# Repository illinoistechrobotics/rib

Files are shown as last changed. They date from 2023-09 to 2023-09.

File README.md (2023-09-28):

# Illinois Tech Robotics - Robot Interface Board (RIB)

This is a PCB design based around the existing Goliath protoboards, but adapted to work with a Raspberry Pi Pico (W), but is also usable with other robot designs using solder bridge jumpers to support various configurations. 

# Features

## Output
The majority of the circuitry allows connecting 2 OSMC's (Open Source Motor Controller) v3.22 over RJ45. They are wired with pin 2 through 9, as CAT6 only has 8 conductors and pin 1 and 10 are the same as 2 and 9 respectively, in this case we don't need the increased current offered by the extra pins.

The 10 connections for the OSMCs are just PWM or digital outputs using MCT9001 Optocouplers, by default set up for 12V (Or whatever is supplied to VIN), but with a jumper it can be set to 5V or 3.3V logic to interface with a variety of motor controllers.

There is a MAX6959 36-channel LED driver chip, that independently controls the 2-digit 7-segment display, the status LEDs of the ethernet ports, and the 3 RGB LEDs present.

## Input
2 rotary quadrature encoders can be connected with RJ45, intended to be used with the Pico's PIO. The RJ45 connections for the encoders have breakouts for Z inputs (for absolute positioning) or 2 more encoders with relative positioning only. These inputs are not connected to the Pico by default due to the limited number of GPIO pins.

There is a MCP3008 ADC which is used for battery voltage & current monitoring.

## I/O

There are 2 PCF8574 I/O expanders which are mostly ununsed, allowing for the connection of low bandwith devices (e.g. enable pins, end stops / limit switches, basic on/off logic) as their speed is limited by the I2C bus. That said, the interrupt pins are broken out and can be optionally used for a decent connection for a rotary encoder.

The first I/O expander is connected to 2 N-channel MOSFETs that are connected to the board's input voltage for VIN @ 2A (total) controllable high-power output.

There are 3 extra GPIO pins exposed, which can be used for connecting e.g. the extra encoder pins, the I/O expander interrupts, or I2C communication to other RIB(s) in order to create a megaRIB for connecting more than 2 OSMCs.

Finally, there is a place for a Digi xBee to sit and communicate with the robot over 2.4Ghz / 900 MHz radio.

## POWER 

Additionally, the PCB pulls power in from the OSMCs over the RJ45 connections or the top left terminal block. The RIB can take in from 8 to 60V of power, or you can provide 5V via headers directly. If it's necessary, the RIB can be powered by a 2S Lithium battery, the power supply can still function at around 7V in.

The onboard 5V switching power supply can provide ~1.8A and the 3v3 regulator, which pulls from the 5V line, can use up to the same 1.8A limit. The 3v3 regulator exists to  provide extra power to the xBee and 3v3 logic without having to put strain on the Pico.

The power inputs on the OSMC RJ45's can also be changed to *output* power and will match the logic voltage 5V/3.3V.

# Programming

The Pi Pico W can be programming with [Arduino-Pico](https://arduino-pico.readthedocs.io/en/latest/), the Pico C++ SDK, Micro/CircuitPython, or Embassy Rust framework. Code examples below are written based on the Arduino-Pico framework. *Note: we discovered a bug in Arduino-Pico's setXX functions affecting the RIB that is only fixed in v3.6.0 or higher.*

Things to know for programming the hardware on the RIB:

The xBee is connected to UART0 / Serial1 on the Pico via pins 16 & 17 for TX & RX respectively. 

	Serial1.setRX(17);
  	Serial1.setTX(16);

The I2C bus for the LED driver and I/O expanders is connected to I2C1 / Wire, pins 20 & 21 for SDA and SCL respectively. 

    Wire.setSDA(20);
    Wire.setSCL(21);

The LED driver has address 0x38. There is no library for the MAX6959 available online, we wrote one in [rib-test-code](https://git.myitr.org/adeck/rib-test-code). Look for lines like `Wire.beginTransmission(0x38)` and functions like `set_digit()` for example.

The I/O expanders have addresses 0x20 for the top one (connected to MOSFETs) and 0x21 for the bottom one.

The library `xreef/PCF8574` has the ability to set pins as well, so the code you would use is

    PCF8574 ioex1(0x20, 20, 21);
    PCF8574 ioex2(0x21, 20, 21);

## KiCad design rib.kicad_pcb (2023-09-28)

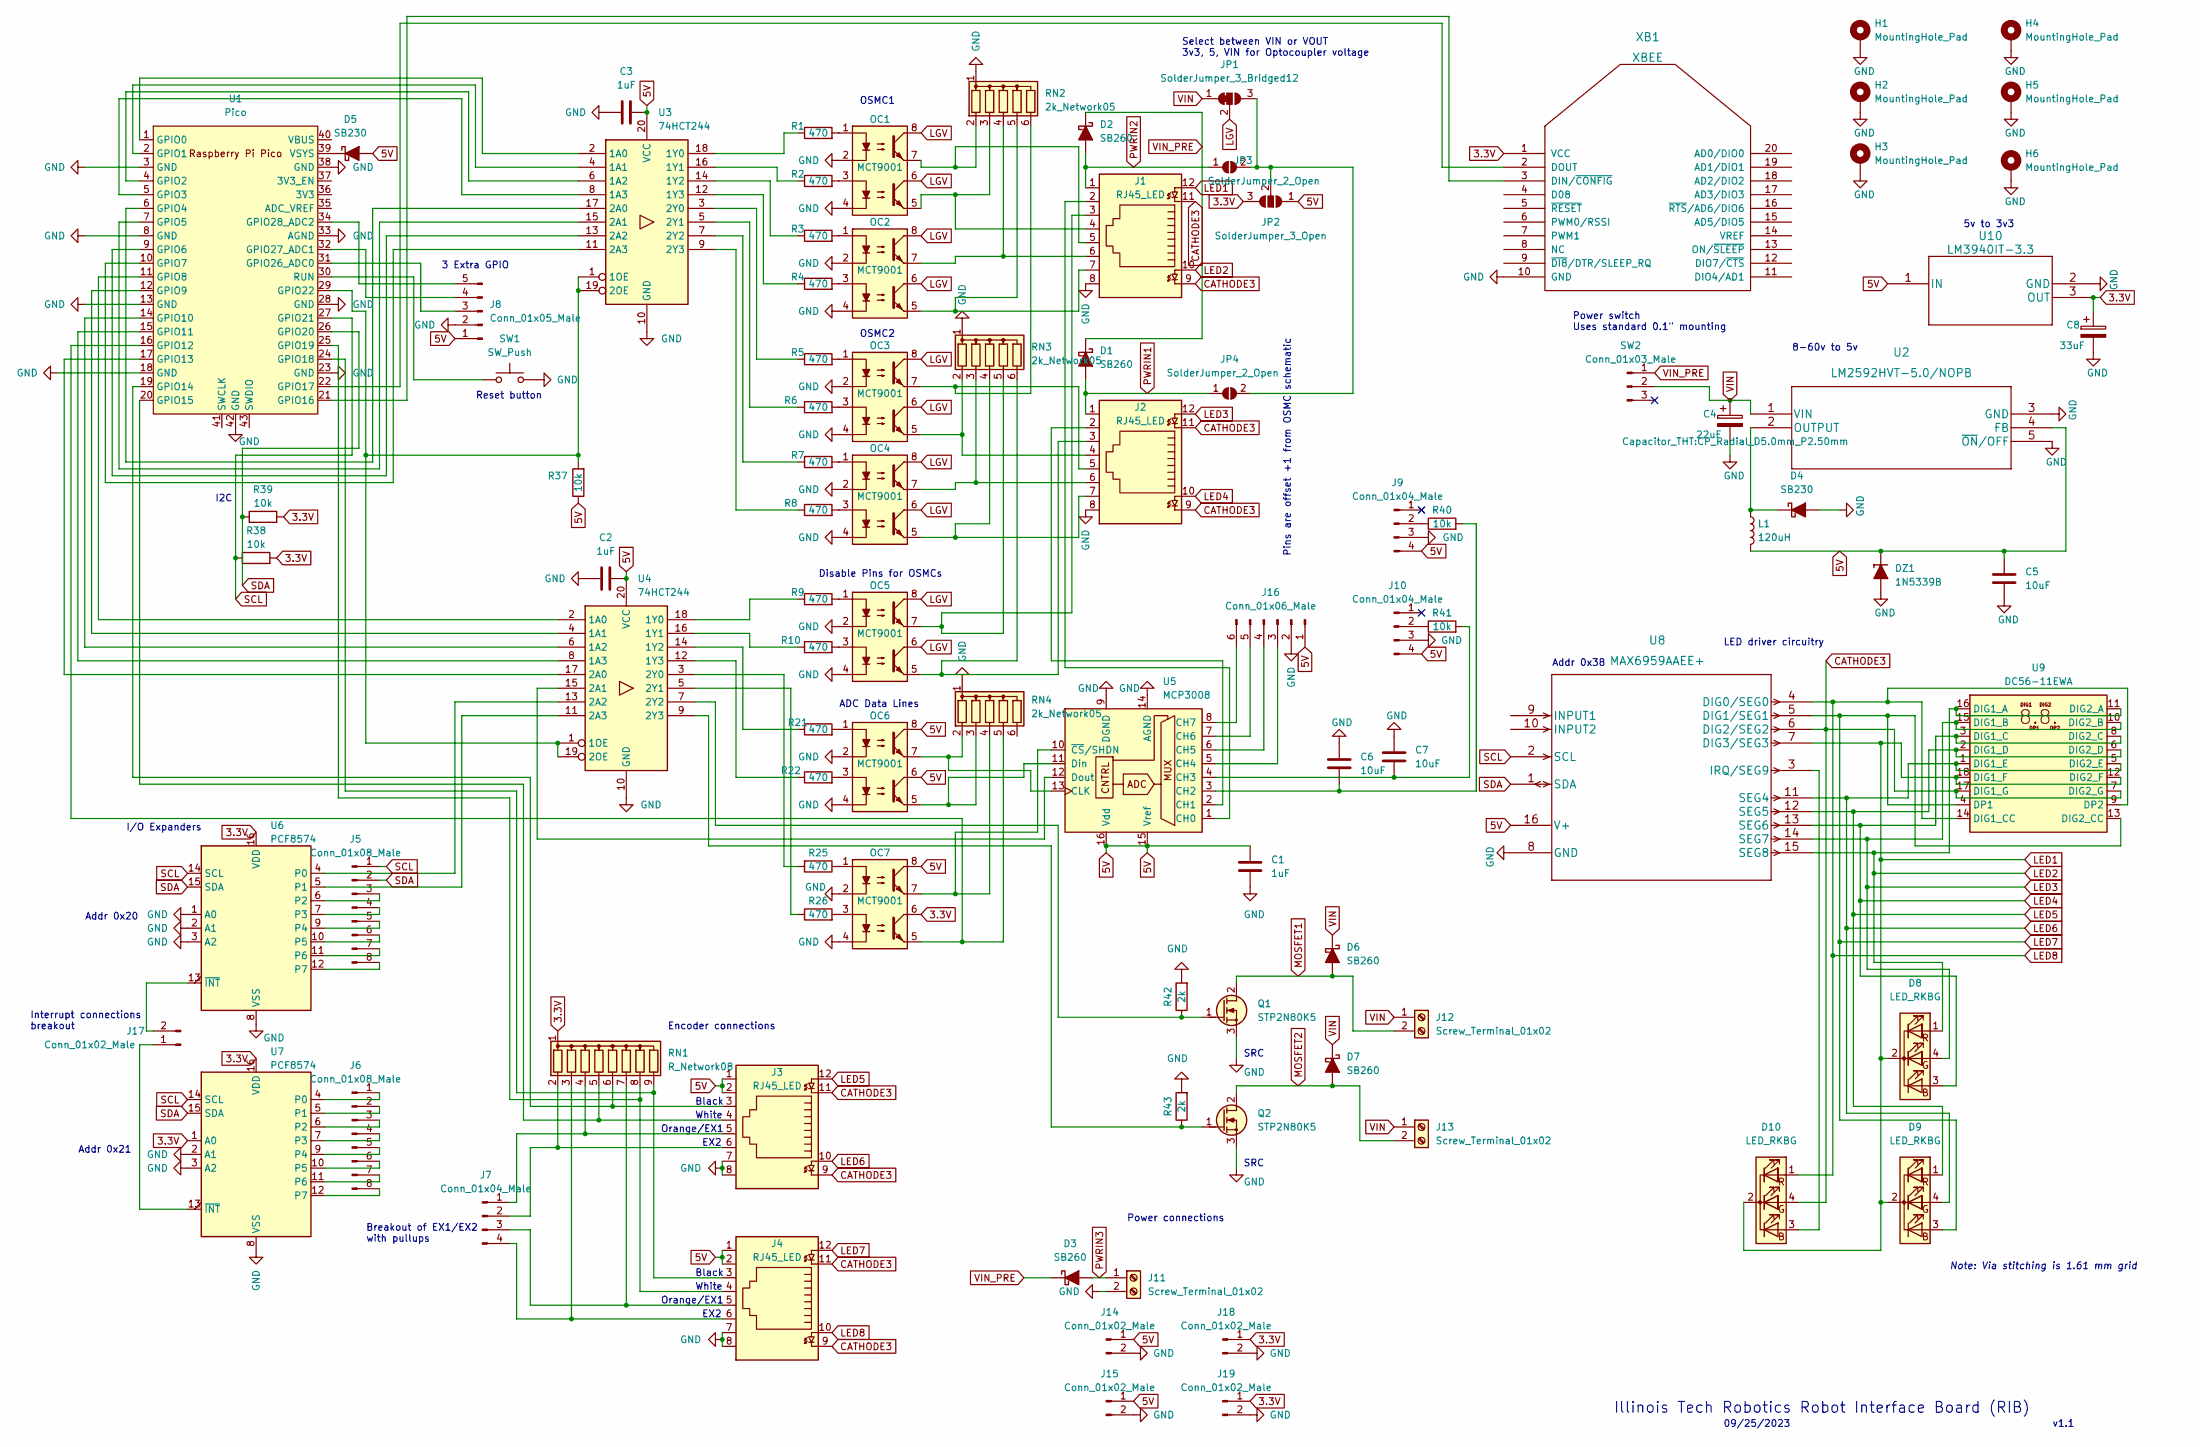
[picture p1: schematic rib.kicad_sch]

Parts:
C1, C2, C3: 1uF; C_Rect_L7.0mm_W4.5mm_P5.00mm
C4: 22uF; CP_Radial_D5.0mm_P2.50mm
C5, C6, C7: 10uF; C_Rect_L7.0mm_W4.5mm_P5.00mm
C8: 33uF; CP_Radial_D5.0mm_P2.50mm
D1, D2, D3, D6, D7: SB260; D_DO-15_P10.16mm_Horizontal
D4, D5: SB230; D_DO-15_P10.16mm_Horizontal
D8, D9, D10: LED_RKBG; LED_D5.0mm-4_RGB_Staggered_Pins
DZ1: 1N5339B; D_5W_CASE-017AA_P12.70mm_Horizontal_Zener
H1, H2, H3, H4, H5, H6: MountingHole_Pad; MountingHole_4.3mm_M4_Pad_Via
J1, J2, J3, J4: RJ45_LED; RJ45_Amphenol_RJHSE538X
J5, J6: Conn_01x08_Male; PinHeader_1x08_P2.54mm_Vertical
J7, J9, J10: Conn_01x04_Male; PinHeader_1x04_P2.54mm_Vertical
J8: Conn_01x05_Male; PinHeader_1x05_P2.54mm_Vertical
J11, J12, J13: Screw_Terminal_01x02; TerminalBlock_Phoenix_MKDS-1,5-2_1x02_P5.00mm_Horizontal
J14, J15, J17, J18, J19: Conn_01x02_Male; PinHeader_1x02_P2.54mm_Vertical
J16: Conn_01x06_Male; PinHeader_1x06_P2.54mm_Vertical
JP1: SolderJumper_3_Bridged12; SolderJumper-3_P1.3mm_Open_Pad1.0x1.5mm
JP2: SolderJumper_3_Open; SolderJumper-3_P1.3mm_Open_Pad1.0x1.5mm
JP3, JP4: SolderJumper_2_Open; SolderJumper-2_P1.3mm_Open_Pad1.0x1.5mm
L1: 120uH; L_Radial_D12.5mm_P7.00mm_Fastron_09HCP
OC1, OC2, OC3, OC4, OC5, OC6, OC7: MCT9001; DIP-8_W7.62mm_Socket
Q1, Q2: STP2N80K5; TO-220-3_Vertical_GDS
R1, R2, R3, R4, R5, R6, R7, R8, R9, R10, R21, R22, R25, R26: 470; R_Axial_DIN0207_L6.3mm_D2.5mm_P10.16mm_Horizontal
R37, R38, R39, R40, R41: 10k; R_Axial_DIN0207_L6.3mm_D2.5mm_P10.16mm_Horizontal
R42, R43: 2k; R_Axial_DIN0207_L6.3mm_D2.5mm_P10.16mm_Horizontal
RN1: R_Network08; R_Array_SIP9
RN2, RN3, RN4: 2k_Network05; R_Array_SIP6
SW1: SW_Push; SW_Tactile_PUSH_4.5mm_H3.8mm_TS_C016
SW2: Conn_01x03_Male; PinSocket_1x03_P2.54mm_Vertical
U1: Pico; RPi_Pico_SMD_TH
U2: LM2592HVT-5.0/NOPB; LM2592HVT-5.0&slash_NOPB
U3, U4: 74HCT244; DIP-20_W7.62mm_Socket
U5: MCP3008; DIP-16_W7.62mm_Socket
U6, U7: PCF8574; DIP-16_W7.62mm_Socket
U8: MAX6959AAEE+; DIP-16_W7.62mm_Socket
U9: DC56-11EWA; DA56-11SURKWA
U10: LM3940IT-3.3; TO-220-3_Vertical
XB1: XBEE; XBEE_PRO_PTH

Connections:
3.3V: C8.1, J18.1, J19.1, JP2.3 (B), OC7.6, R38.2, R39.2, RN1.1 (common), U6.16 (VDD), U7.1 (A0), U7.16 (VDD), U10.3 (OUT), XB1.1 (VCC)
5V: C1.1, C2.2, C3.2, C5.1, D5.2 (A), DZ1.1 (K), J3.1, J3.2, J4.1, J4.2, J8.1, J9.4, J10.4, J14.1, J15.1, J16.1, JP2.1 (A), L1.2, OC6.6, OC6.8, OC7.8, R37.1, U2.4 (FB), U3.20 (VCC), U4.20 (VCC), U5.15 (Vref), U5.16 (Vdd), U8.16 (V+), U10.1 (IN)
CATHODE3: D10.4 (GA), J1.9, J1.11, J2.9, J2.11, J3.9, J3.11, J4.9, J4.11, U8.6 (DIG2/SEG2), U9.7 (DIG2_G), U9.17 (DIG1_G)
GND: C1.2, C2.1, C3.1, C4.2, C5.2, C6.1, C7.1, C8.2, D4.2 (A), DZ1.2 (A), H1.1, H2.1, H3.1, H4.1, H5.1, H6.1, J1.8, J2.8, J3.7, J3.8, J4.7, J4.8, J8.2, J9.3, J10.3, J11.2, J14.2, J15.2, J16.2, J18.2, J19.2, OC1.2, OC1.4, OC2.2, OC2.4, OC3.2, OC3.4, OC4.2, OC4.4, OC5.2, OC5.4, OC6.2, OC6.4, OC7.2, OC7.4, Q1.3 (S), Q2.3 (S), R42.2, R43.2, RN2.1 (common), RN3.1 (common), RN4.1 (common), SW1.2, U1.3 (GND), U1.8 (GND), U1.13 (GND), U1.18 (GND), U1.23 (GND), U1.28 (GND), U1.33 (AGND), U1.38 (GND), U1.42 (GND), U2.3 (GND), U2.5 (~ON/OFF), U3.10 (GND), U4.10 (GND), U5.9 (DGND), U5.14 (AGND), U6.1 (A0), U6.2 (A1), U6.3 (A2), U6.8 (VSS), U7.2 (A1), U7.3 (A2), U7.8 (VSS), U8.8 (GND), U10.2 (GND), XB1.10 (GND)
LED1: D8.2 (K), D9.2 (K), D10.2 (K), J1.12, U8.7 (DIG3/SEG3), U9.12 (DIG2_F), U9.18 (DIG1_F)
LED2: D8.1 (RA), J1.10, U8.15 (SEG8), U9.11 (DIG2_A), U9.16 (DIG1_A)
LED3: D8.4 (GA), J2.12, U8.14 (SEG7), U9.10 (DIG2_B), U9.15 (DIG1_B)
LED4: D8.3 (BA), J2.10, U8.13 (SEG6), U9.3 (DIG1_C), U9.8 (DIG2_C)
LED5: D9.1 (RA), J3.12, U8.12 (SEG5), U9.2 (DIG1_D), U9.6 (DIG2_D)
LED6: D9.4 (GA), J3.10, U8.11 (SEG4), U9.1 (DIG1_E), U9.5 (DIG2_E)
LED7: D9.3 (BA), J4.12, U8.5 (DIG1/SEG1), U9.4 (DP1), U9.13 (DIG2_CC)
LED8: D10.1 (RA), J4.10, U8.4 (DIG0/SEG0), U9.9 (DP2), U9.14 (DIG1_CC)
LGV: JP1.2 (C), OC1.6, OC1.8, OC2.6, OC2.8, OC3.6, OC3.8, OC4.6, OC4.8, OC5.6, OC5.8
MOSFET1: D6.2 (A), J12.2, Q1.2 (D)
MOSFET2: D7.2 (A), J13.2, Q2.2 (D)
unnamed: D4.1 (K), L1.1, U2.2 (OUTPUT)
unnamed: D5.1 (K), U1.39 (VSYS)
unnamed: D10.3 (BA), U8.3 (IRQ/SEG9)
unnamed: J5.3, U6.6 (P2)
unnamed: J5.4, U6.7 (P3)
unnamed: J5.5, U6.9 (P4)
unnamed: J5.6, U6.10 (P5)
unnamed: J5.7, U6.11 (P6)
unnamed: J5.8, U6.12 (P7)
unnamed: J6.1, U7.4 (P0)
unnamed: J6.2, U7.5 (P1)
unnamed: J6.3, U7.6 (P2)
unnamed: J6.4, U7.7 (P3)
unnamed: J6.5, U7.9 (P4)
unnamed: J6.6, U7.10 (P5)
unnamed: J6.7, U7.11 (P6)
unnamed: J6.8, U7.12 (P7)
unnamed: J3.5, J7.1, RN1.4 (R3)
unnamed: J3.6, J7.2, RN1.2 (R1)
unnamed: J4.5, J7.3, RN1.7 (R6)
unnamed: J4.6, J7.4, RN1.3 (R2)
unnamed: J8.3, U1.31 (GPIO26_ADC0)
unnamed: J8.4, U1.32 (GPIO27_ADC1)
unnamed: J8.5, U1.34 (GPIO28_ADC2)
unnamed: J9.2, R40.1
unnamed: J10.2, R41.1
unnamed: J16.3, U5.5 (CH4)
unnamed: J16.4, U5.6 (CH5)
unnamed: J16.5, U5.7 (CH6)
unnamed: J16.6, U5.8 (CH7)
unnamed: J17.1, U7.13 (~INT)
unnamed: J17.2, U6.13 (~INT)
unnamed: JP1.3 (B), JP2.2 (C), JP3.2 (B), JP4.2 (B)
unnamed: OC1.1, R1.2
unnamed: OC1.3, R2.2
unnamed: OC2.1, R3.2
unnamed: OC2.3, R4.2
unnamed: OC3.1, R5.2
unnamed: OC3.3, R6.2
unnamed: OC4.1, R7.2
unnamed: OC4.3, R8.2
unnamed: OC5.1, R9.2
unnamed: OC5.3, R10.2
unnamed: OC6.1, R21.2
unnamed: OC6.3, R22.2
unnamed: OC7.1, R25.1
unnamed: OC7.3, R26.2
unnamed: Q1.1 (G), R42.1, U4.7 (2Y2)
unnamed: Q2.1 (G), R43.1, U4.9 (2Y3)
unnamed: J3.4, RN1.5 (R4), U1.20 (GPIO15)
unnamed: J3.3, RN1.6 (R5), U1.19 (GPIO14)
unnamed: J4.4, RN1.8 (R7), U1.25 (GPIO19)
unnamed: J4.3, RN1.9 (R8), U1.24 (GPIO18)
unnamed: J1.5, OC1.7, RN2.2 (R1)
unnamed: J1.4, OC1.5, RN2.3 (R2)
unnamed: J1.6, OC2.7, RN2.4 (R3)
unnamed: J1.7, OC2.5, RN2.5 (R4)
unnamed: J2.5, OC3.7, RN2.6 (R5)
unnamed: J2.4, OC3.5, RN3.2 (R1)
unnamed: J2.6, OC4.7, RN3.3 (R2)
unnamed: J2.7, OC4.5, RN3.4 (R3)
unnamed: J1.3, OC5.7, RN3.5 (R4)
unnamed: J2.3, OC5.5, RN3.6 (R5)
unnamed: OC6.7, RN4.2 (R1), U5.13 (CLK)
unnamed: OC6.5, RN4.3 (R2), U5.11 (Din)
unnamed: OC7.7, RN4.4 (R3), U5.10 (~CS/SHDN)
unnamed: OC7.5, RN4.5 (R4), U1.16 (GPIO12)
unnamed: U1.1 (GPIO0), U3.2 (1A0)
unnamed: U1.2 (GPIO1), U3.4 (1A1)
unnamed: U1.4 (GPIO2), U3.6 (1A2)
unnamed: U1.5 (GPIO3), U3.8 (1A3)
unnamed: U1.6 (GPIO4), U3.17 (2A0)
unnamed: U1.7 (GPIO5), U3.15 (2A1)
unnamed: U1.9 (GPIO6), U3.13 (2A2)
unnamed: U1.10 (GPIO7), U3.11 (2A3)
unnamed: U1.11 (GPIO8), U4.2 (1A0)
unnamed: U1.12 (GPIO9), U4.4 (1A1)
unnamed: U1.14 (GPIO10), U4.6 (1A2)
unnamed: U1.15 (GPIO11), U4.8 (1A3)
unnamed: U1.17 (GPIO13), U4.17 (2A0)
unnamed: U1.21 (GPIO16), XB1.3 (DIN/~CONFIG)
unnamed: U1.22 (GPIO17), XB1.2 (DOUT)
unnamed: R37.2, U1.29 (GPIO22), U3.1 (1OE), U3.19 (2OE), U4.1 (1OE), U4.19 (2OE)
unnamed: SW1.1, U1.30 (RUN)
unnamed: R1.1, U3.18 (1Y0)
unnamed: R2.1, U3.16 (1Y1)
unnamed: R3.1, U3.14 (1Y2)
unnamed: R4.1, U3.12 (1Y3)
unnamed: R5.1, U3.3 (2Y0)
unnamed: R6.1, U3.5 (2Y1)
unnamed: R7.1, U3.7 (2Y2)
unnamed: R8.1, U3.9 (2Y3)
unnamed: R9.1, U4.18 (1Y0)
unnamed: R10.1, U4.16 (1Y1)
unnamed: R21.1, U4.14 (1Y2)
unnamed: R22.1, U4.12 (1Y3)
unnamed: U4.15 (2A1), U5.12 (Dout)
unnamed: U4.13 (2A2), U6.4 (P0)
unnamed: U4.11 (2A3), U6.5 (P1)
unnamed: R25.2, U4.3 (2Y0)
unnamed: R26.1, U4.5 (2Y1)
unnamed: J1.2, U5.1 (CH0)
unnamed: J2.2, U5.2 (CH1)
unnamed: C6.2, R40.2, U5.3 (CH2)
unnamed: C7.2, R41.2, U5.4 (CH3)
PWRIN1: D1.2 (A), J2.1, JP4.1 (A)
PWRIN2: D2.2 (A), J1.1, JP3.1 (A)
PWRIN3: D3.2 (A), J11.1
SCL: J5.1, R38.1, U1.27 (GPIO21), U6.14 (SCL), U7.14 (SCL), U8.2 (SCL)
SDA: J5.2, R39.1, U1.26 (GPIO20), U6.15 (SDA), U7.15 (SDA), U8.1 (SDA)
VIN: C4.1, D6.1 (K), D7.1 (K), J12.1, J13.1, JP1.1 (A), SW2.2, U2.1 (VIN)
VIN_PRE: D1.1 (K), D2.1 (K), D3.1 (K), SW2.1

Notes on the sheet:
Reset button
Encoder connections
Black
I/O Expanders
Interrupt connections breakout
Power connections
5v to 3v3
3 Extra GPIO
Disable Pins for OSMCs
White
Illinois Tech Robotics Robot Interface Board (RIB)
OSMC2
OSMC1
ADC Data Lines
8-60v to 5v
Select between VIN or VOUT 3v3, 5, VIN for Optocoupler voltage
LED driver circuitry
SRC
Orange/EX1
Breakout of EX1/EX2 with pullups
09/25/2023
EX2
Note: Via stitching is 1.61 mm grid
Pins are offset +1 from OSMC schematic
Addr 0x20
Addr 0x38
I2C
Power switch Uses standard 0.1" mounting
v1.1
Addr 0x21

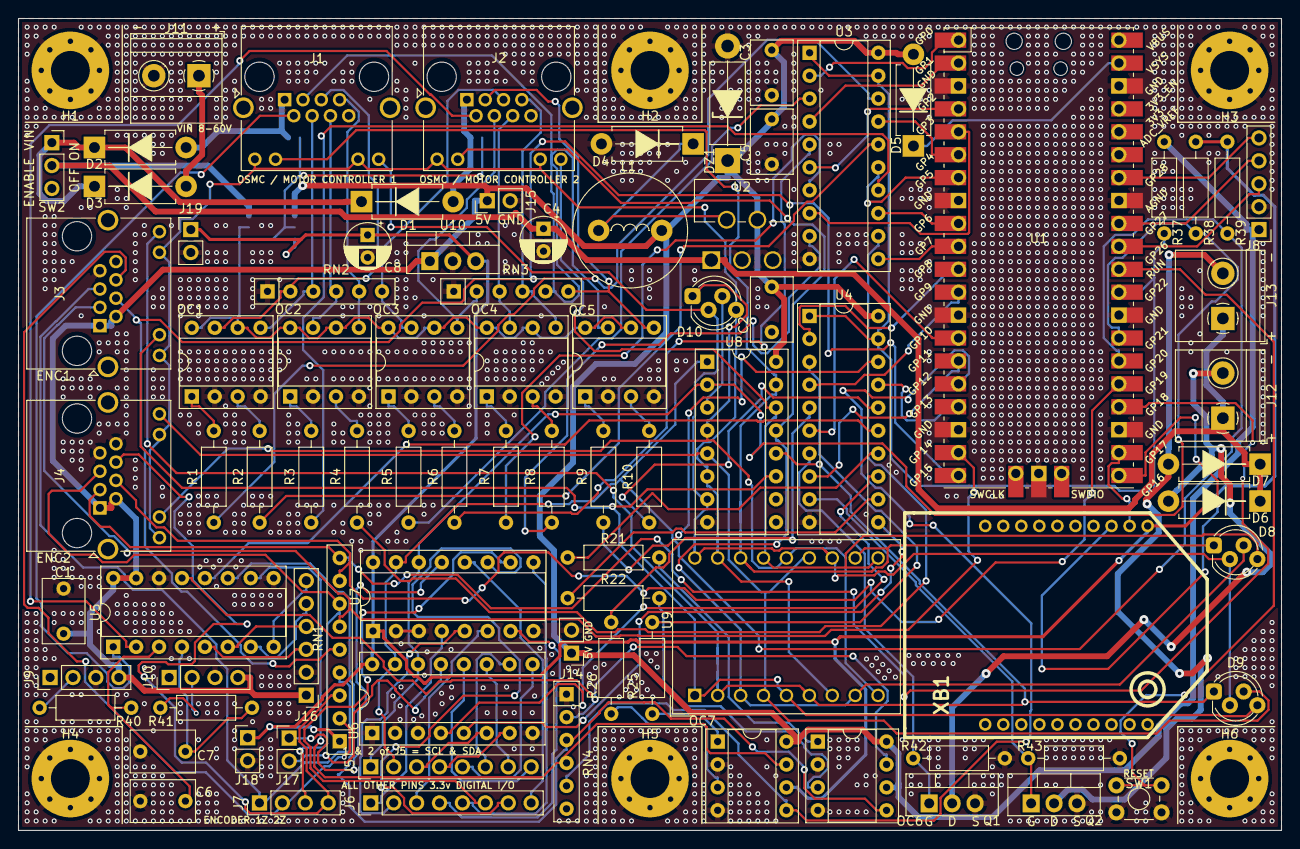
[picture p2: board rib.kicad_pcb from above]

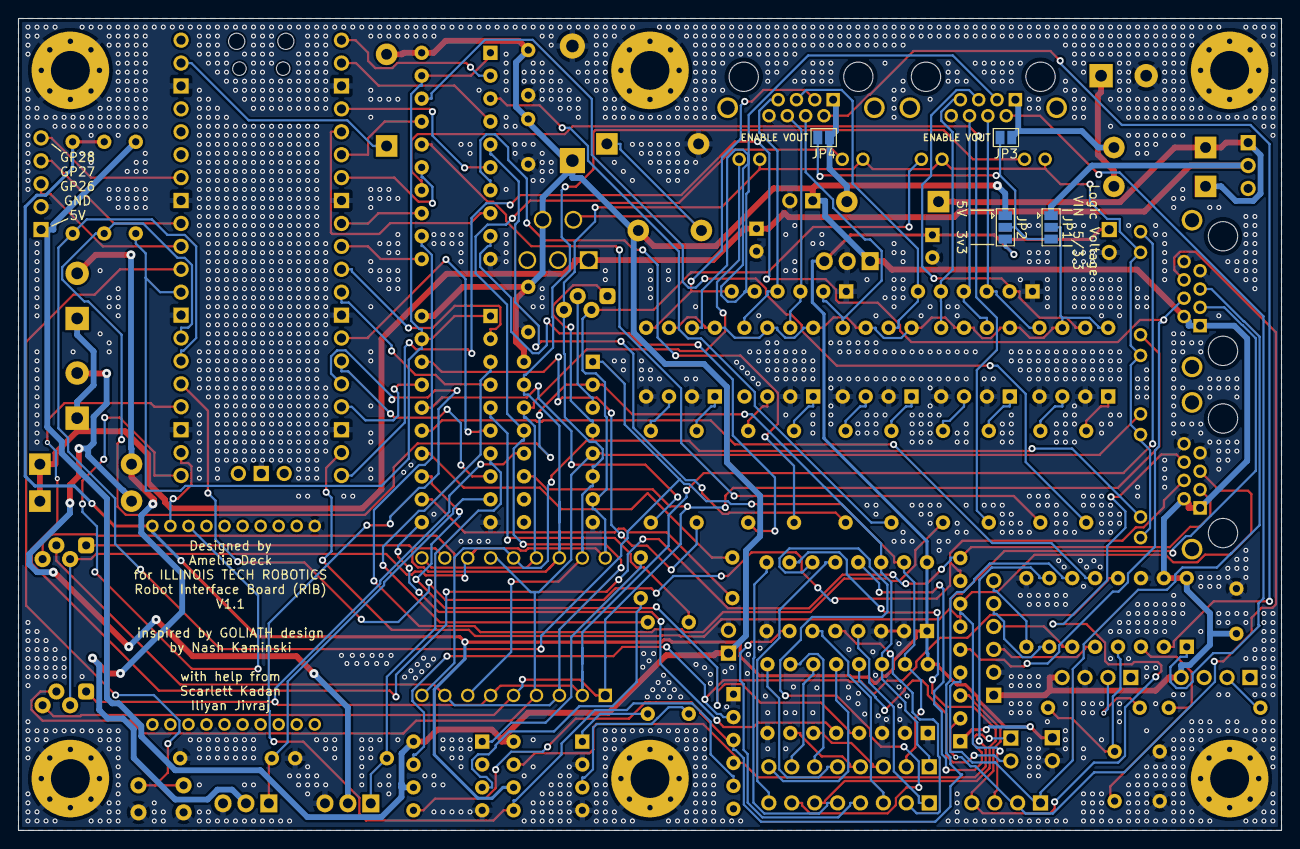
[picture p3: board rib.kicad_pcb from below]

Board: 2 copper layers, 140.0 x 90.0 mm, 96 parts (4 on the bottom side), 127 nets.

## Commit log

2023-02-14 Initial PCB start
    [goliath_pcb.kicad_pcb, goliath_pcb.kicad_sch]
2023-02-15 Add ADC for battery monitoring
    [goliath_pcb.kicad_pcb, goliath_pcb.kicad_sch]
2023-02-15 Add LTC1798 ADC on PCB
    [goliath_pcb.kicad_pcb, goliath_pcb.kicad_sch]
2023-02-15 Verify all connections, add 7805
    [goliath_pcb.kicad_pcb, goliath_pcb.kicad_sch]
2023-02-15 Small tweak
    [goliath_pcb.kicad_pcb]
2023-02-15 Move IC5 in line with other chips to avoid overlapping silkscreen
    [goliath_pcb.kicad_pcb]
2023-02-15 Remove extra text
    [goliath_pcb.kicad_pcb]
2023-02-15 Add buffers, restart PCB layout, start encoder stuff
    [goliath_pcb.kicad_pcb, goliath_pcb.kicad_sch]
2023-02-16 Layout PCB
    [goliath_pcb.kicad_pcb, goliath_pcb.kicad_sch]
2023-02-16 Plan for xbee support
    [goliath_pcb.kicad_sch]
2023-02-16 Add xBee initial plan
    [goliath_pcb.kicad_pcb, goliath_pcb.kicad_sch]
2023-02-20 Run traces for current version
    [goliath_pcb.kicad_pcb, goliath_pcb.kicad_sch]
2023-02-20 Add extra I/O and extra headers, expand PCB
    [goliath_pcb.kicad_pcb, goliath_pcb.kicad_sch]
2023-03-06 Add more resistors, caps
    [goliath_pcb.kicad_pcb, goliath_pcb.kicad_sch]
2023-03-07 Add mosfets and stuff
    [goliath_pcb.kicad_pcb, goliath_pcb.kicad_sch]
2023-03-07 Finish mosfet circuits, add grounding vias, mark at potential orderable prototype (add BOM)
    [goliath_pcb.kicad_pcb, goliath_pcb.kicad_sch]
2023-03-07 Actually connect MOSFETs to logic outputs
    [goliath_pcb.kicad_pcb, goliath_pcb.kicad_sch]
2023-03-08 Add comments via silkscreen, start to use alternative kicad library
    [goliath_pcb.kicad_pcb, goliath_pcb.kicad_sch]
2023-03-08 Add some symbol replacements
    [goliath_pcb.kicad_sch]
2023-03-08 Swap out all optocouplers (symbols, not the actual part)
    [goliath_pcb.kicad_pcb, goliath_pcb.kicad_sch]
2023-03-08 Clean up schematic
    [goliath_pcb.kicad_pcb, goliath_pcb.kicad_sch]
2023-03-08 Update BOM
2023-03-08 Add proper M4 mounting holes
    [goliath_pcb.kicad_pcb, goliath_pcb.kicad_sch]
2023-03-09 Fix silkscreen issues
    [goliath_pcb.kicad_pcb]
2023-03-10 Prepare to swap out diodes
    [goliath_pcb.kicad_pcb]
2023-03-10 Switch to better diodes, use via stitching plugin
    [goliath_pcb.kicad_pcb, goliath_pcb.kicad_sch]
2023-03-10 Adjust via stitching to alighn with silkscreen text
    [goliath_pcb.kicad_pcb, goliath_pcb.kicad_sch]
2023-03-10 Fix other silkscreen text
    [goliath_pcb.kicad_pcb]
2023-03-10 Remove extra vias
    [goliath_pcb.kicad_pcb]
2023-03-10 More via work
    [goliath_pcb.kicad_pcb]
2023-03-10 BIG inductor
    [goliath_pcb.kicad_pcb, goliath_pcb.kicad_sch]
2023-03-10 Prepare RC1 for purchase
    [goliath_pcb.kicad_pcb, goliath_pcb.kicad_sch]
2023-03-10 Add a reset button, plan for power switch
    [goliath_pcb.kicad_pcb, goliath_pcb.kicad_sch]
2023-03-10 Add power switch, add more text, cleanup
    [goliath_pcb.kicad_pcb, goliath_pcb.kicad_sch]
2023-03-10 Rename project
    [rib.kicad_pcb, rib.kicad_sch]
2023-03-10 RIBodified: rib.kicad_prl
    [rib.kicad_pcb]
2023-03-10 Add Digi-Key parts list
    [RIB-v1.0-RC1.csv]
2023-03-11 Oh yeah, resistor networks exist
    [rib.kicad_pcb, rib.kicad_sch]
2023-03-11 Start adding led driver
    [rib.kicad_pcb, rib.kicad_sch]
2023-03-11 Add 7seg, LED driver, connect LEDs. Fix BOM & add LEDs tomorrow
    [rib.kicad_pcb, rib.kicad_sch]
2023-03-20 Small changes
    [rib.kicad_pcb]
2023-03-20 Add RGB LEDs
    [rib.kicad_pcb, rib.kicad_sch]
2023-03-20 Fix keepouts for screwholes, update parts list
    [RIB-v1.0-RC1.csv, rib.kicad_pcb]
2023-03-20 Update CSV Digi-Key BOM
    [RIB-v1.0-RC1.csv]
2023-03-21 Fix duplicate part
    [RIB-v1.0-RC1.csv]
2023-03-22 Update to kicad 7.0
    [rib.kicad_pcb, rib.kicad_sch]
2023-03-26 Fix xbee connection visuals
    [rib.kicad_pcb, rib.kicad_sch]
2023-03-30 Fix issues with RC1 - LED orientation, pullups, 3v3 source
    [rib.kicad_pcb, rib.kicad_sch]
2023-03-30 Reroute with better trace thickness
    [rib.kicad_pcb]
2023-03-30 Fix track hole clearance. crashes when trying to do via stitching
    [rib.kicad_pcb]
2023-03-31 Make space for heatsinks
    [rib.kicad_pcb]
2023-03-31 Fix via stitching
    [rib.kicad_pcb]
2023-03-31 Update BOM (new 7seg CC, 3v3 reg LM3940, 33 uF cap), add lib
2023-03-31 Add Digi-Key BOMs for v1.0
    [RIB-v1.0 Upgrade w_ permanents.csv, RIB-v1.0 Upgrade.csv, RIB-v1.0-RC1_BAD.csv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]
2023-04-01 prepare to add zener diode
    [rib.kicad_pcb, rib.kicad_sch]
2023-05-18 v1.0 design update (BOMs not updated)
    [rib.kicad_pcb, rib.kicad_sch]
2023-09-28 RIB v1.1 pre-release, documentation
    [rib.kicad_pcb, rib.kicad_sch]
